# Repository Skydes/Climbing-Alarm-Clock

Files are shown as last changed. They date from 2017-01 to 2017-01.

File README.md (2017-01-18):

# Climbing alarm clock

We introduce here a new prototype of alarm clock which aims at helping people who find it difficult to get up in the morning, also known as *snooze addicts*.

## Concept

The snooze button of a standard alarm clock allows to postpone the ringing time by a predefined number of minutes. Overusing it while staying in bed may lead to oversleeping, with many associated issues.

In the proposed solution, the snooze button is suspended to a string above the bed and moves upward as the button is pressed several times. At the point where it is too high, the user has no other possibility than to get out of bed to stop the alarm. This eventually forces him to find motivation to wake up.

## Features

* Customisable ringtone (RTTTL standard)
* Easily and fully configurable through a screen with intuitive GUI
* Cheap and easy-to-find components

## Technical aspects

The button is moved up and down by a string rolled around an endless screw which is linked to a motor with encoder.
The sound is produced by a simple buzzer.
The OLED screen is associated with push buttons whose bounces are removed by a resistor- and capacitor-based low-pass filter.
The system accurately keeps track of time using a Real Time Clock (RTC) that remains accurate even when it is plugged out.

Bill of Material:

* PRismino microcontroller
* PRisme shield
* BO-10 DC motor
* Didel encoder
* SH1106 OLED
* DS3231 RTC
* 5V DC transformer
* 3D-printed parts

Wiring for the microcontroller:

| Pin		| Connection		|
| :---:	| :---:			|
| D0		| *Previous* button	|
| D1		| *OK* button		|
| D2		| I2C SDA			|
| D3 		| I2C SCL 			|
| D4 		| RTC interrupt 	|
| D7 		| *Next* button 	|
| D8 		| Buzzer 			|
| A2 		| OLED SCK 		|
| A3 		| OLED SDA 		|
| A4 		| OLED DC 			|
| A5		| OLED CS 			|
| SCK		| *Snooze* button 	|
| MOSI	| Encoder 1 		|
| MISO	| Encoder 2 		|

Required software libraries:

* [Robopoly’s PRismino](https://github.com/Robopoly/Robopoly_PRismino)
* [U8glib](https://github.com/olikraus/u8glib)
* [RTClib](https://github.com/jcw/rtclib)
  * For the DS3231, one might have to modify the following lines in `RTClib.cpp`:
    * `#define DS1307_CONTROL_REGISTER 0x0E`
    * `#define RTC_DS1307__RS0         0x03`
    * `#define RTC_DS1307__RS1         0x04`
    * `#define RTC_DS1307__SQWE        0x06`

## Credits
This project has been developed by Paul-Edouard Sarlin with the support of Robopoly.

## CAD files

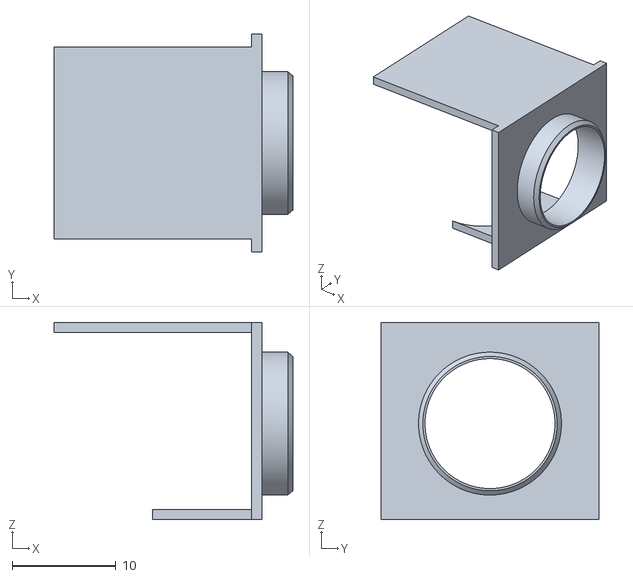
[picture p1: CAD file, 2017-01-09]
src_3d/STL CUBE INF.stl
23.0 x 21.0 x 19.0

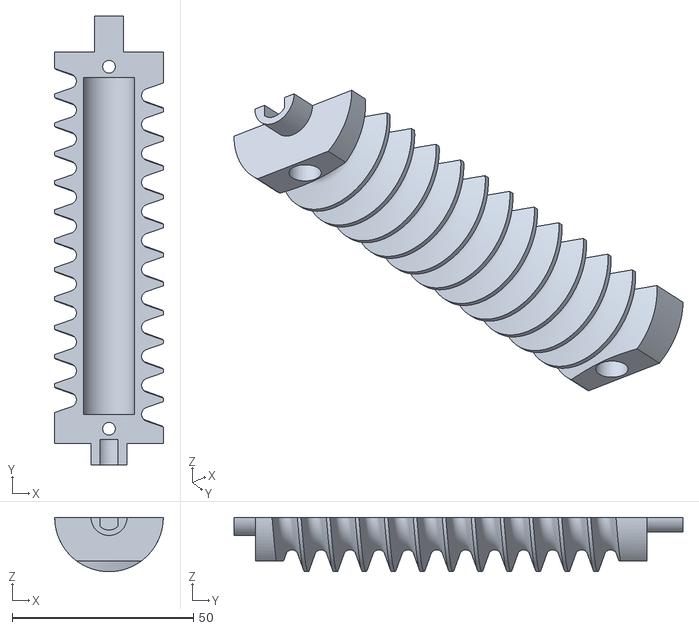
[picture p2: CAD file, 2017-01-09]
src_3d/STL VIS PARTIE2.stl
30.0 x 124.0 x 15.0

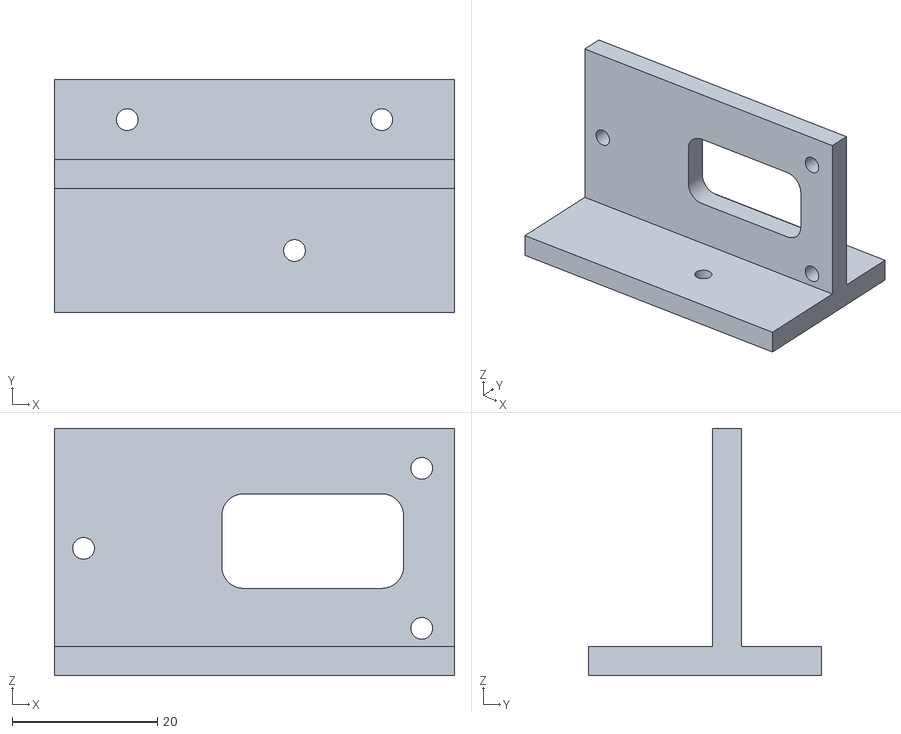
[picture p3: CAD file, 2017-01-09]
src_3d/STL SUPPORT MOTEUR.stl
55.0 x 32.0 x 34.0

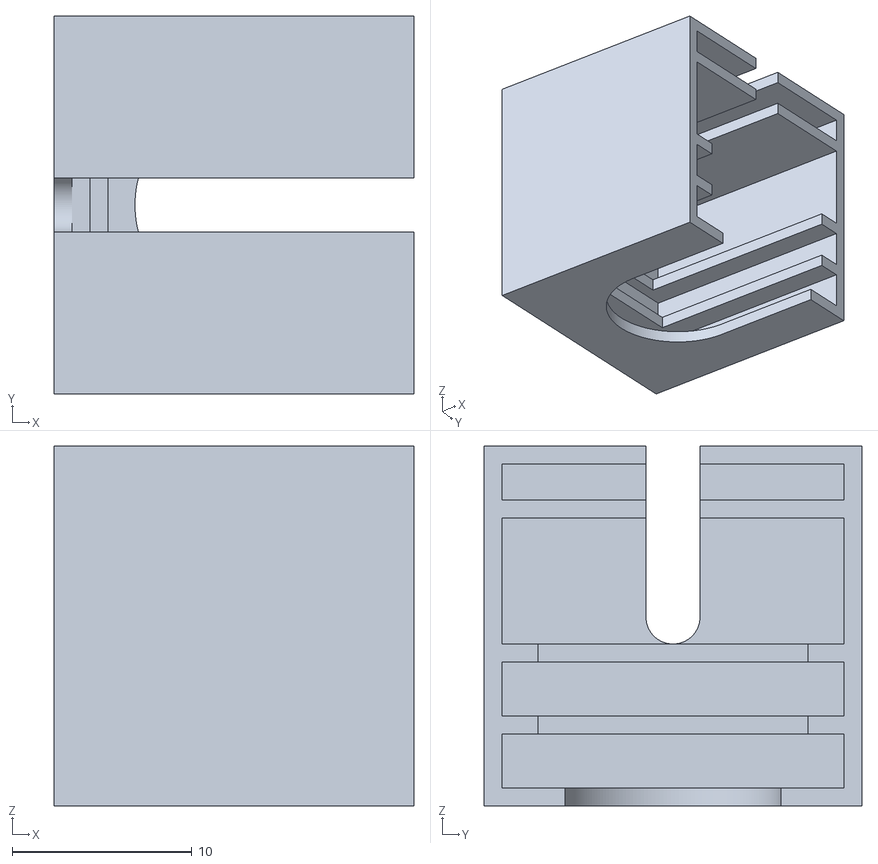
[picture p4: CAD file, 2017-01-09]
src_3d/STL CUBE SUP.stl
20.0 x 21.0 x 20.0

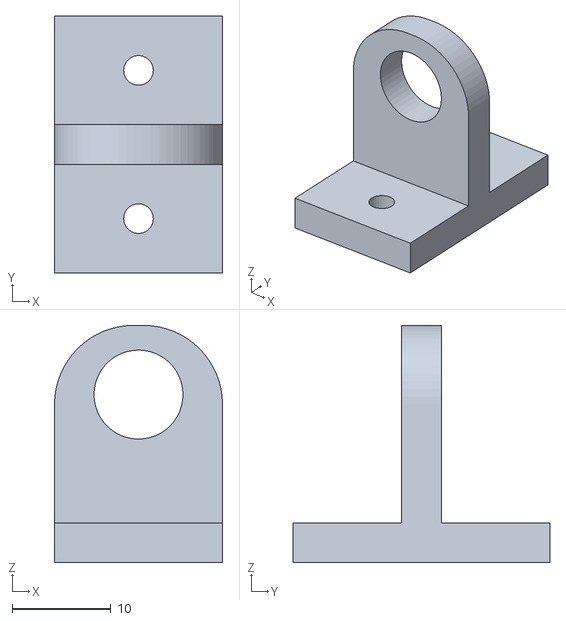
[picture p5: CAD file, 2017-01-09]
src_3d/STL SUPPORT AXE.stl
17.0 x 26.0 x 24.0

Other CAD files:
src_3d/STL VIS PARTIE1.stl
src_3d/CUBE_SNOOZE.CATProduct
src_3d/CUBE_SNOOZE_INF.CATPart
src_3d/CUBE_SNOOZE_SUP.CATPart
src_3d/SUPPORT_AXE.CATPart
src_3d/SUPPORT_MOTEUR.CATPart

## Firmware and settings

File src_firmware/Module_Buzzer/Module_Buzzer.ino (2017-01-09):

 /***************************************************************************************
 *
 * Copyright (c) 2017, Paul-Edouard Sarlin
 * All rights reserved.
 *
 * Title:       Climbing Alarm Clock Project
 * File:        Module_Buzzer.ino
 * Date:        2017-01-09
 * Author:      Paul-Edouard Sarlin
 * Website:     https://github.com/Skydes/Climbing-Alarm-Clock
 *
 * Description: Independant module for Buzzer control.
 *
 ***************************************************************************************/
 
 #include <prismino.h>

#define SONGS_NUMBER  4
#define OCTAVE_OFFSET -1
#define isdigit(n) (n >= '0' && n <= '9')

int notes[] = { 0,
262, 277, 294, 311, 330, 349, 370, 392, 415, 440, 466, 494,
523, 554, 587, 622, 659, 698, 740, 784, 831, 880, 932, 988,
1047, 1109, 1175, 1245, 1319, 1397, 1480, 1568, 1661, 1760, 1865, 1976,
2093, 2217, 2349, 2489, 2637, 2794, 2960, 3136, 3322, 3520, 3729, 3951
};

byte default_dur;
byte default_oct;
int bpm;
int num;
long wholenote;
long duration;
byte note;
byte scale;

char *song_Mario = "Mario:d=4,o=5,b=100:16e6,16e6,32p,8e6,16c6,8e6,8g6,8p,8g,8p,8c6,16p,8g,16p,8e,16p,8a,8b,16a#,8a,16g.,16e6,16g6,8a6,16f6,8g6,8e6,16c6,16d6,8b,16p,8c6,16p,8g,16p,8e,16p,8a,8b,16a#,8a,16g.,16e6,16g6,8a6,16f6,8g6,8e6,16c6,16d6,8b,8p,16g6,16f#6,16f6,16d#6,16p,16e6,16p,16g#,16a,16c6,16p,16a,16c6,16d6,8p,16g6,16f#6,16f6,16d#6,16p,16e6,16p,16c7,16p,16c7,16c7,p,16g6,16f#6,16f6,16d#6,16p,16e6,16p,16g#,16a,16c6,16p,16a,16c6,16d6,8p,16d#6,8p,16d6,8p,16c6";
char *song_SW_main = "SW_main:d=4,o=5,b=45:32p,32f#,32f#,32f#,8b.,8f#.6,32e6,32d#6,32c#6,8b.6,16f#.6,32e6,32d#6,32c#6,8b.6,16f#.6,32e6,32d#6,32e6,8c#.6,32f#,32f#,32f#,8b.,8f#.6,32e6,32d#6,32c#6,8b.6,16f#.6,32e6,32d#6,32c#6,8b.6,16f#.6,32e6,32d#6,32e6,8c#6";
char *song_SW_cantina = "SW_cantina:d=4,o=5,b=250:8a,8p,8d6,8p,8a,8p,8d6,8p,8a,8d6,8p,8a,8p,8g#,a,8a,8g#,  8a,g,8f#,8g,8f#,f.,8d.,16p,p.,8a,8p,8d6,8p,8a,8p,8d6,8p,8a,8d6,8p,8a,8p,8g#,8a,8p, 8g,8p,g.,8f#,8g,8p,8c6,a#,a,g";
char *song_SW_end = "SW_end:d=4,o=5,b=225:2c,1f,2g.,8g#,8a#,1g#,2c.,c,2f.,g,g#,c,8g#.,8c.,8c6,1a#.,2c,2f.,g,g#.,8f,c.6,8g#,1f6,2f,8g#.,8g.,8f,2c6,8c.6,8g#.,8f,2c,8c.,8c.,8c,2f,8f.,8f.,8f,2f";
//char *song_Zelda = "Zelda:d=4,o=5,b=125:a#,f.,8a#,16a#,16c6,16d6,16d#6,2f6,8p,8f6,16f.6,16f#6,16g#.6,2a#.6,16a#.6,16g#6,16f#.6,8g#.6,16f#.6,2f6,f6,8d#6,16d#6,16f6,2f#6,8f6,8d#6,8c#6,16c#6,16d#6,2f6,8d#6,8c#6,8c6,16c6,16d6,2e6,g6,8f6,16f,16f,8f,16f,16f,8f,16f,16f,8f,8f,a#,f.,8a#,16a#,16c6,16d6,16d#6,2f6,8p,8f6,16f.6,16f#6,16g#.6,2a#.6,c#7,c7,2a6,f6,2f#.6,a#6,a6,2f6,f6,2f#.6,a#6,a6,2f6,d6,2d#.6,f#6,f6,2c#6,a#,c6,16d6,2e6,g6,8f6,16f,16f,8f,16f,16f,8f,16f,16f,8f,8f";
//char *song_Bond = "Bond:d=4,o=5,b=80:32p,16c#6,32d#6,32d#6,16d#6,8d#6,16c#6,16c#6,16c#6,16c#6,32e6,32e6,16e6,8e6,16d#6,16d#6,16d#6,16c#6,32d#6,32d#6,16d#6,8d#6,16c#6,16c#6,16c#6,16c#6,32e6,32e6,16e6,8e6,16d#6,16d6,16c#6,16c#7,c.7,16g#6,16f#6,g#.6";

char *songs[SONGS_NUMBER] = {song_Mario, song_SW_main, song_SW_cantina, song_SW_end}; //, song_Zelda, song_Bond};
volatile uint8_t song_current = 0;

volatile bool stop_song_flag = false;

void setup() 
{ }

char* song_setup(char *p)
{
  while(*p != ':') p++;    // ignore name
  p++;                     // skip ':'
  
  if(*p == 'd') // get default duration
  {
    p++; p++;              // skip "d="
    num = 0;
    while(isdigit(*p))
    {
      num = (num * 10) + (*p++ - '0');
    }
    if(num > 0) default_dur = num;
    p++;                   // skip comma
  }
  
  if(*p == 'o') // get default octave
  {
    p++; p++;              // skip "o="
    num = *p++ - '0';
    if(num >= 3 && num <=7) default_oct = num;
    p++;                   // skip comma
  }
 
  if(*p == 'b') // get BPM
  {
    p++; p++;              // skip "b="
    num = 0;
    while(isdigit(*p))
    {
      num = (num * 10) + (*p++ - '0');
    }
    bpm = num;
    p++;                   // skip colon
  }
 
  // BPM usually expresses the number of quarter notes per minute
  wholenote = (60 * 1000L / bpm) * 4;  // this is the time for whole note (in milliseconds)

  return p;
}

bool song_play()
{
  default_dur = 4, default_oct = 6, bpm = 63; // initialize default variables
  char *p = songs[song_current];
  p = song_setup(p);
  
  while(*p)
  {
    num = 0;
    while(isdigit(*p)) // first, get note duration, if available
    {
      num = (num * 10) + (*p++ - '0');
    }
    
    if(num) duration = wholenote / num;
    else duration = wholenote / default_dur;  // we will need to check if we are a dotted note after
 
    note = 0; // now get the note
    switch(*p)
    {
      case 'c':
        note = 1;
        break;
      case 'd':
        note = 3;
        break;
      case 'e':
        note = 5;
        break;
      case 'f':
        note = 6;
        break;
      case 'g':
        note = 8;
        break;
      case 'a':
        note = 10;
        break;
      case 'b':
        note = 12;
        break;
      case 'p':
      default:
        note = 0;
    }
    p++;
 
    if(*p == '#') // now, get optional '#' sharp
    {
      note++;
      p++;
    }
 
    if(*p == '.') // now, get optional '.' dotted note
    {
      duration += duration/2;
      p++;
    }
  
    if(isdigit(*p)) // now, get scale
    {
      scale = *p - '0';
      p++;
    }
    else
    {
      scale = default_oct;
    }
 
    scale += OCTAVE_OFFSET;
 
    if(*p == ',')
      p++;       // skip comma for next note (or we may be at the end)
 
    if(note) // now play the note
    {
      tone(BUZZER, notes[(scale - 4) * 12 + note]);
      delay(duration);
      noTone(BUZZER);
    }
    else
      delay(duration);

    if(stop_song_flag)
      return false;
  }
  return true;
}

void loop() 
{
  if(!song_play())
    while(1);
}

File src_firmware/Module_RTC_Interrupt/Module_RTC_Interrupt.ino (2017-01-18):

 /***************************************************************************************
 *
 * Copyright (c) 2017, Paul-Edouard Sarlin
 * All rights reserved.
 *
 * Title:       Climbing Alarm Clock Project
 * File:        Module_RTC_Interrupt.ino
 * Date:        2017-01-09
 * Author:      Paul-Edouard Sarlin
 * Website:     https://github.com/Skydes/Climbing-Alarm-Clock
 *
 * Description: Module for the interrupt-based RTC.
 *
 ***************************************************************************************/

#include <Wire.h>
#include <prismino.h>
#include <RTClib.h>

#define SQW_READ    ((PIND >> 4) & 1)
#define COMMUTE_LED (PORTC ^= (1 << 7))

RTC_DS1307 RTC;

volatile unsigned counter = 0;
volatile bool redraw_required = false;

void setup() 
{
  // ICP1 interrupt settings
  TCCR1B |= (1 << ICNC1) | (1 << ICES1);
  TIMSK1 |= (1 << ICIE1);
  sei();
  
  Wire.begin();
  RTC.begin();
  Serial.begin(9600); // debug
  pinMode(LED, OUTPUT); // debug
  COMMUTE_LED;

  RTC.setSqwOutSignal(RTC_DS1307::Frequency_1Hz);
}

void loop() 
{
  if(redraw_required)
  {
    Serial.println(counter);
    redraw_required = false;
  }
}

ISR(TIMER1_CAPT_vect)
{
  COMMUTE_LED;
  if(SQW_READ)
  {
    counter++;
    redraw_required = true;
  }
}

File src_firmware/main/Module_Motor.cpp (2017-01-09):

 /***************************************************************************************
 *
 * Copyright (c) 2017, Paul-Edouard Sarlin
 * All rights reserved.
 *
 * Title:       Climbing Alarm Clock Project
 * File:        Module_Motor.cpp
 * Date:        2017-01-09
 * Author:      Paul-Edouard Sarlin
 * Website:     https://github.com/Skydes/Climbing-Alarm-Clock
 *
 ***************************************************************************************/

#include "Module_Motor.h"

#define B_SN_READ ((PINB >> 1) & 1)
#define ENC1_ON   !(PINB & (1 << 2))
#define ENC2_ON   !(PINB & (1 << 3))

#define SNOOZE_STEPS  2736 // one wheel turn
#define LENGTH_P_TURN 8   // centimeters
#define LENGTH_TOT    70  // centimeters
#define LENGTH_MIN    1   // centimeters
#define MAX_POS       LENGTH_TOT/LENGTH_P_TURN*SNOOZE_STEPS

volatile int enc_position = 0; // total position
volatile int goal_position = 0;
uint8_t snooze_length = 15; // centimeters
volatile bool b_sn_state = false; // used to select interrupt triggers
extern volatile bool rolling_out = false;


enum {e0, e1, e2, e3};
volatile uint8_t enc_next_state = e0;

volatile uint8_t mot_state = M_STOPPED;


void Mot_setup()
{
  // Pin Change interrupts setup
  PCICR |= (1 << PCIE0); // enable PCINT0 interrupt vector
  PCMSK0 |= (1 << PCINT1) | (1 << PCINT2) | (1 << PCINT3);
  SREG |= (1 << 7);
  
  // DDRB &= 0b01110000; // PB7, 6 ,5, 4 in input mode
}

uint8_t Mot_get_sn_dist()
{
  return snooze_length;
}

uint8_t Mot_set_sn_dist(int8_t new_dist)
{
  if(new_dist < LENGTH_MIN)
    snooze_length = LENGTH_TOT - new_dist;
  else if(new_dist > LENGTH_TOT)
    snooze_length = new_dist - LENGTH_TOT;
  else
    snooze_length = new_dist;
}

void Mot_check_pos()
{
  if( ((mot_state == M_UP) && (enc_position > goal_position)) || ((mot_state == M_DOWN) && (enc_position < goal_position)) )
  {
    MOTOR_OFF;
    mot_state = M_STOPPED;
    rolling_out = false;
  }
}

void Mot_set_next_pos()
{
  if(!rolling_out)
  {
    goal_position = enc_position + (unsigned)snooze_length/LENGTH_P_TURN*SNOOZE_STEPS;
    if(goal_position > MAX_POS)
      goal_position = MAX_POS;
  }
  else
    goal_position = 0;
}

ISR(PCINT0_vect)
{
  if(B_SN_READ != b_sn_state)
  {
    b_sn_state = B_SN_READ;

    if( b_sn_state && (global_state == S_RINGING) )
    {
      global_state = S_SNOOZED;
      RTC_set_last_snooze();
      Mot_set_next_pos();
    }
  }
  else
  {
    switch(enc_next_state) 
    {
    case e0: 
      if (ENC1_ON) {enc_position++; enc_next_state = e1; }
      if (ENC2_ON) {enc_position--; enc_next_state = e3; }
      break;
    case e1: 
      if (ENC2_ON)  {enc_position++; enc_next_state = e2; }
      if (!ENC1_ON) {enc_position--; enc_next_state = e0; }
      break;
    case e2: 
      if (!ENC1_ON) {enc_position++; enc_next_state = e3; }
      if (!ENC2_ON) {enc_position--; enc_next_state = e1; }
      break;
    case e3:
      if (!ENC2_ON) {enc_position++; enc_next_state = e0; }
      if (ENC1_ON)  {enc_position--; enc_next_state = e2; }
      break; 
    }
  }
}
